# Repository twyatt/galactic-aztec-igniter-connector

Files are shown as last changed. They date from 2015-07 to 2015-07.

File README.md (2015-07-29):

# About
OSHPark PCB Top Thumbnail
OSHPark PCB Bottom Thumbnail

Custom board used to convert igniter ethernet plugs to 2-position terminal blocks for the [Galactic Aztec] rocket. The board was designed to interface with the [Galactic Aztec Raspberry Pi Add-on: Igniter] board.

Custom EagleCAD parts on this board can be found in the [SDSU Rocket Eagle Libraries].

## Wiring
The ethernet ports adhere to the following [T-568B] wiring configurations:

### Igniter
| Pin | Color | Function |
|:---:|:---:|:---:|
| 1 | Orange/White | Supply Voltage |
| 2 | Orange | Ground |
| 3 | Green/White  | Supply Voltage |
| 4 | Blue | Ground |
| 5 | Blue/White | Supply Voltage |
| 6 | Green | Ground |
| 7 | Brown/White  | Supply Voltage |
| 8 | Brown | Ground |

### Break Wire
| Pin | Color | Function |
|:---:|:---:|:---:|
| 1 | Orange/White | 3.3V |
| 2 | Orange | Signal |
| 3 | Green/White  | 3.3V |
| 4 | Blue | Signal |
| 5 | Blue/White | 3.3V |
| 6 | Green | Signal |
| 7 | Brown/White  | 3.3V |
| 8 | Brown | Signal |

## Launch
For the [Galactic Aztec April 18th, 2015 launch], a strand of solder was screwed into one side of the terminal block labeled "Break" then run thru the igniter and back to the other side of the "Break" terminal block. The "Break" terminal block does not have a polarity and simply opens or closes the connection between 3.3V and Signal.

# Bill of Materials
| Qty | Description | Part Number | Vendor |
|:---:|---|---:|---|
| 1 | Jack RJ45 CAT5/CAT5e | [380-1046-ND] | DigiKey  |
| 1 | LED Red Vf=1.8V If=2mA 0603 | [475-1195-2-ND] | DigiKey  |
| 1 | Resistor 12kΩ 1/4W 1% 0603 | [RHM12.0KADCT-ND] | DigiKey  |
| 3 | Terminal Block 0.2" Pitch Plug | [A98223-ND] | DigiKey  |
| 3 | Terminal Block 0.2" Pitch Socket | [A98235-ND] | DigiKey  |

[Galactic Aztec]: http://rocket.sdsu.edu/rockets
[Galactic Aztec Raspberry Pi Add-on: Igniter]: https://github.com/twyatt/galactic-aztec-rpi-addon-igniter
[SDSU Rocket Eagle Libraries]: https://github.com/twyatt/SDSURocket-Eagle-Libraries
[T-568B]: https://en.wikipedia.org/wiki/TIA/EIA-568#Wiring
[Galactic Aztec April 18th, 2015 launch]: https://github.com/twyatt/galactic-aztec-launch-data
[380-1046-ND]: http://www.digikey.com/product-detail/en/SS-7188-NF/380-1046-ND/388308
[475-1195-2-ND]: http://www.digikey.com/product-detail/en/LS%20L29K-H1J2-1-Z/475-1195-1-ND/810356
[RHM12.0KADCT-ND]: http://www.digikey.com/product-detail/en/ESR03EZPF1202/RHM12.0KADCT-ND/1983756
[A98223-ND]: http://www.digikey.com/product-detail/en/796634-2/A98223-ND/1827082
[A98235-ND]: http://www.digikey.com/product-detail/en/796638-2/A98235-ND/1827094

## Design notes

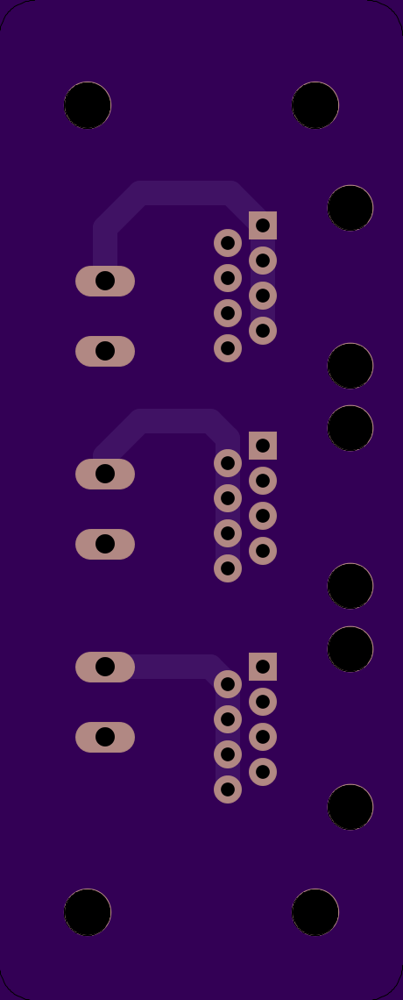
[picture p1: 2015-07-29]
artwork/bottom.png

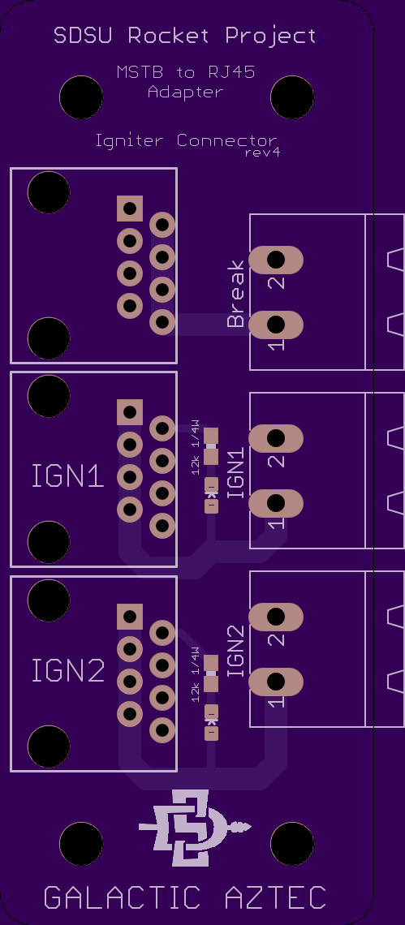
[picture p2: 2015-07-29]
artwork/top.png

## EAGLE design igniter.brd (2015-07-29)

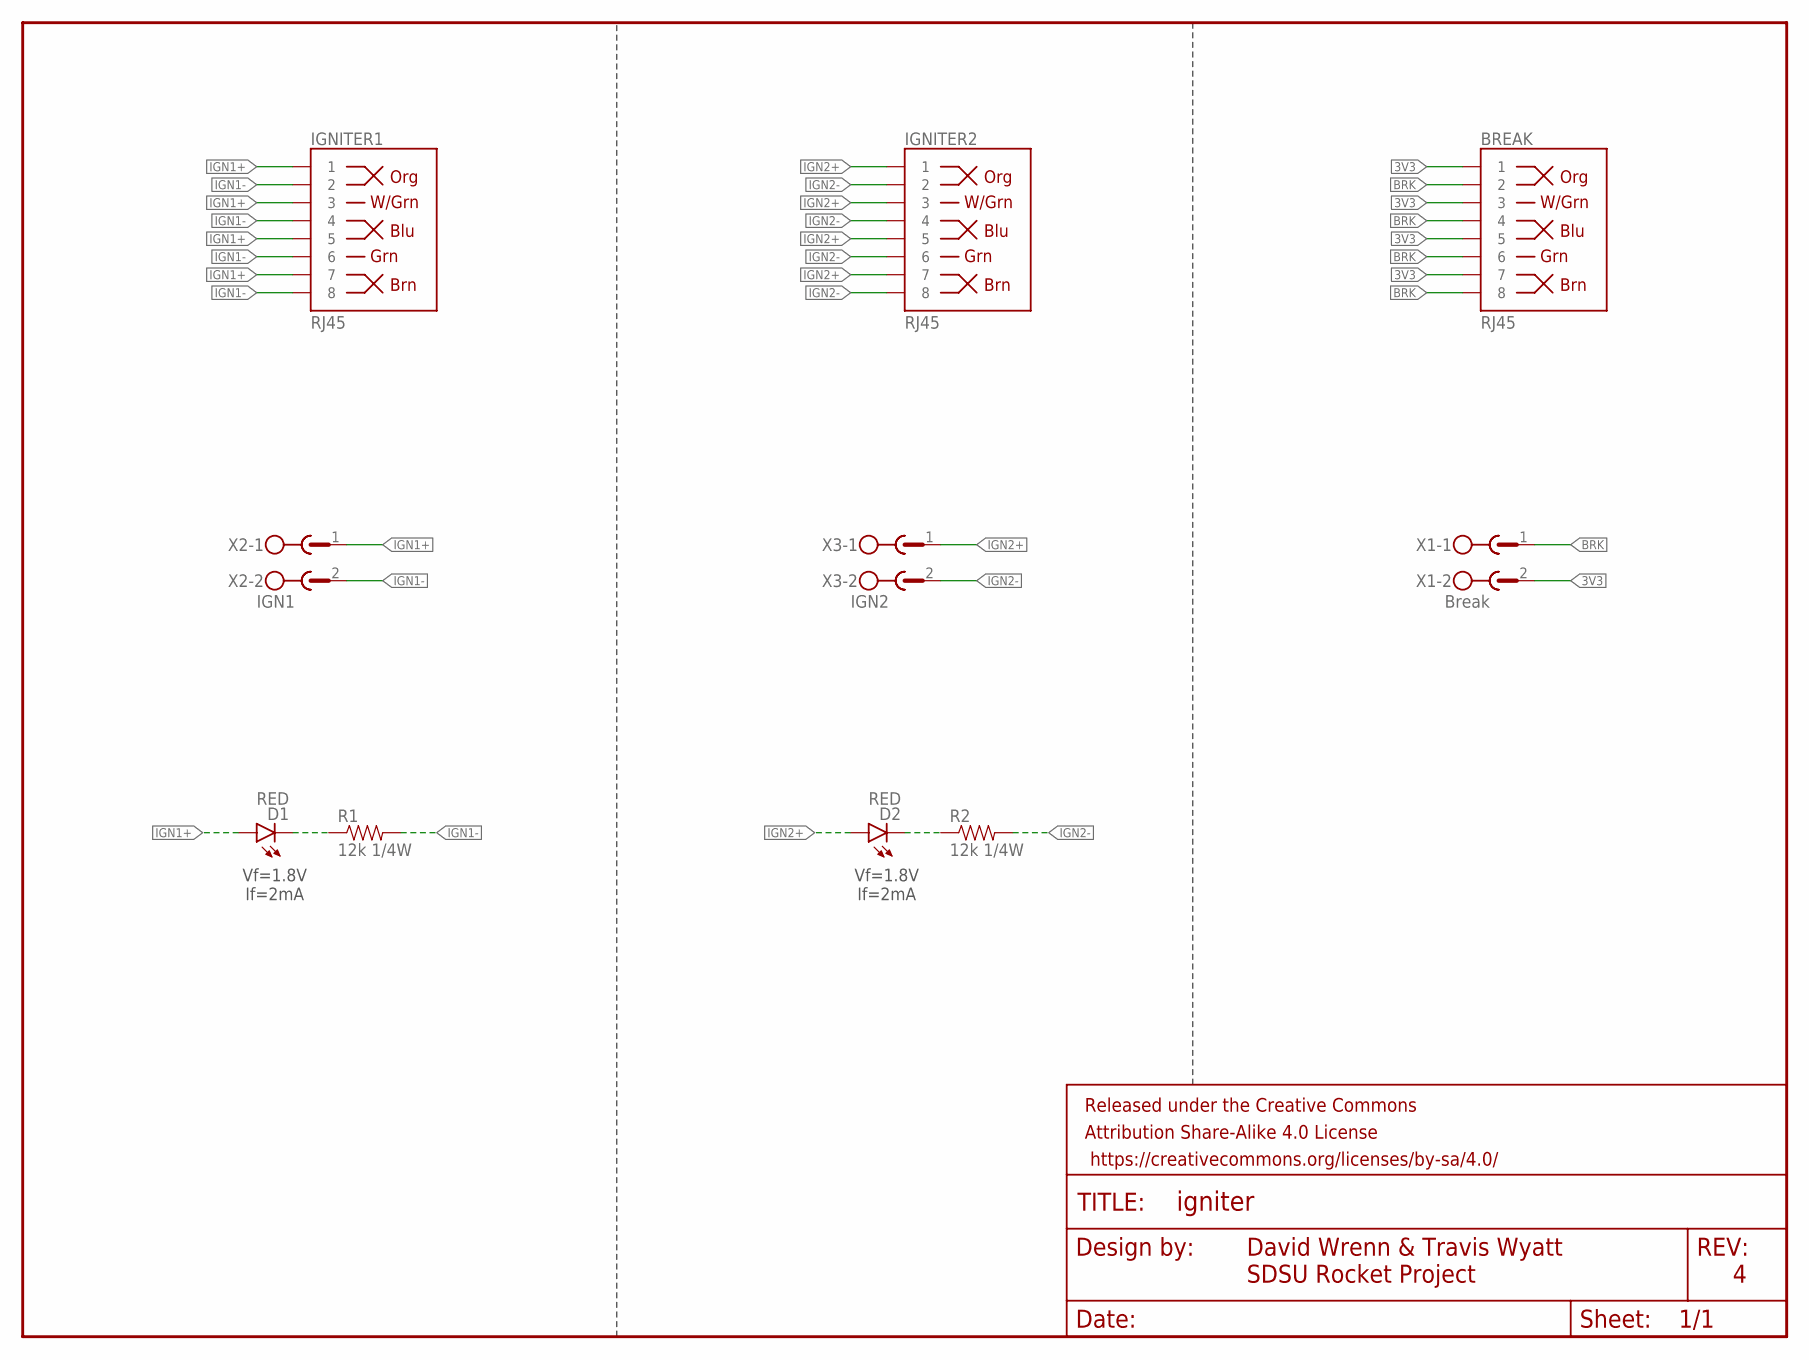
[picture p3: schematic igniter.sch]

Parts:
BREAK: RJ45; RJ45-8
D1, D2: RED; LED-0603
FRAME1: FRAME-LETTER; CREATIVE_COMMONS
IGNITER1, IGNITER2: RJ45; RJ45-8
R1, R2: 12k 1/4W; 0603-RES
X1: Break; MSTBA2
X2: IGN1; MSTBA2
X3: IGN2; MSTBA2

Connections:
3V3: BREAK.1, BREAK.3, BREAK.5, BREAK.7, X1.2
BRK: BREAK.2, BREAK.4, BREAK.6, BREAK.8, X1.1
IGN1+: D1.A, IGNITER1.1, IGNITER1.3, IGNITER1.5, IGNITER1.7, X2.1
IGN1-: IGNITER1.2, IGNITER1.4, IGNITER1.6, IGNITER1.8, R1.2, X2.2
IGN2+: D2.A, IGNITER2.1, IGNITER2.3, IGNITER2.5, IGNITER2.7, X3.1
IGN2-: IGNITER2.2, IGNITER2.4, IGNITER2.6, IGNITER2.8, R2.2, X3.2
unnamed: D1.C, R1.1
unnamed: D2.C, R2.1

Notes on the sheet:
David Wrenn & Travis Wyatt
SDSU Rocket Project
Vf=1.8V If=2mA

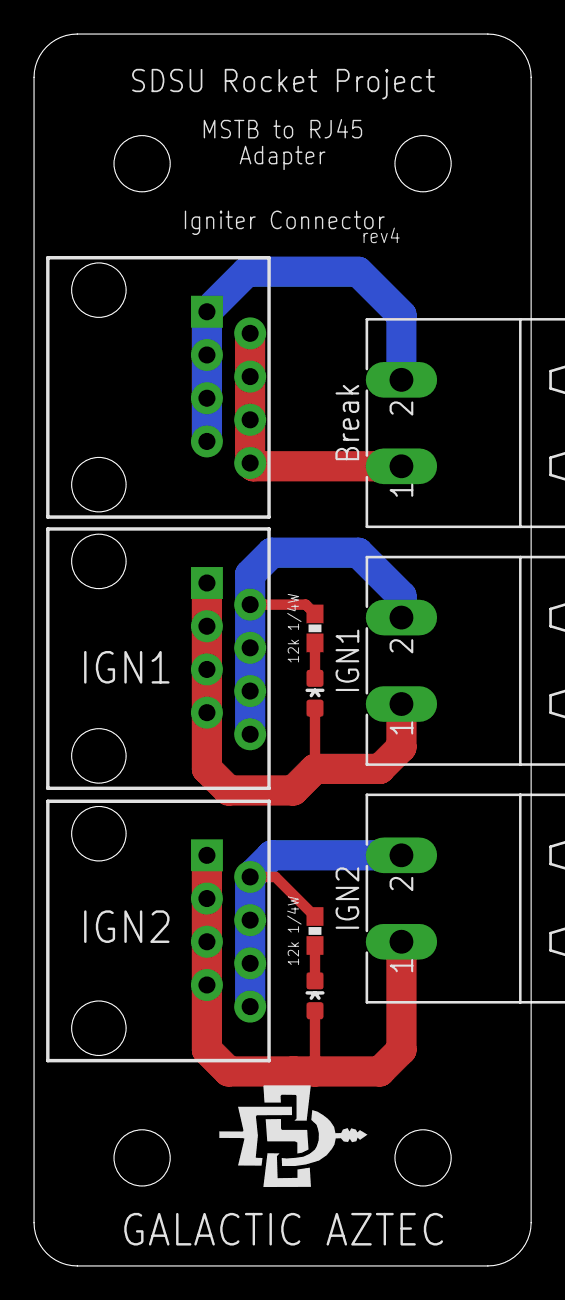
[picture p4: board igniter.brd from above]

Board: 2 copper layers, 29.2 x 72.4 mm, 15 parts (0 on the bottom side), 8 nets.

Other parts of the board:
U$1, U$2, U$3, U$4: STAND-OFF

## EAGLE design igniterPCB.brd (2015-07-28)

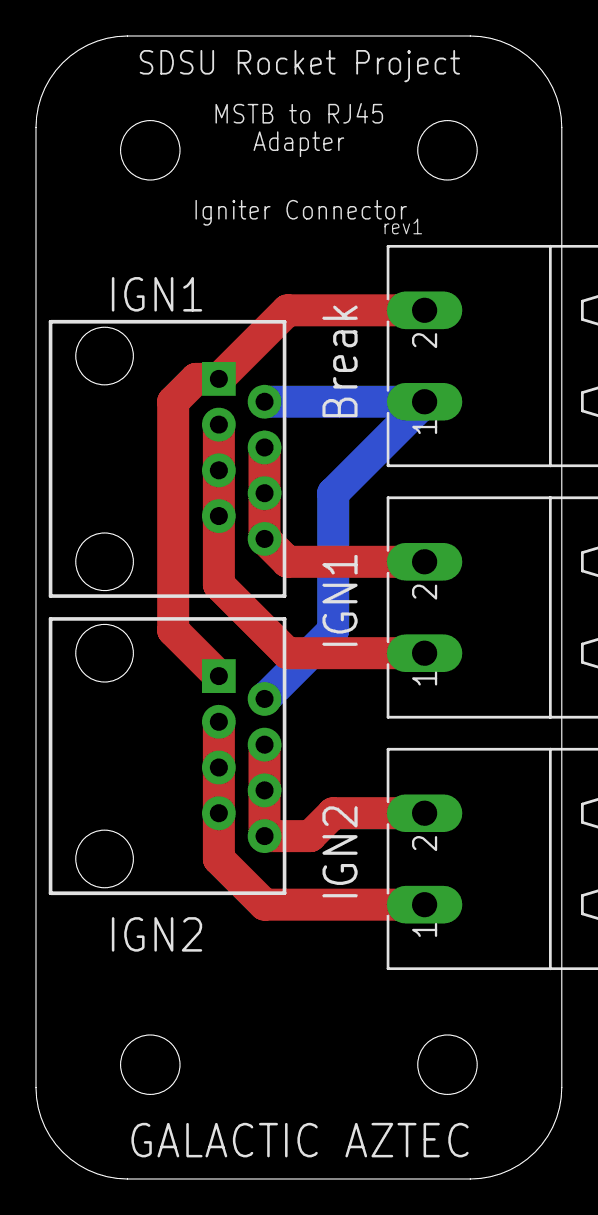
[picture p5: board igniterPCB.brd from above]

Board: 2 copper layers, 29.2 x 63.5 mm, 9 parts (0 on the bottom side), 6 nets.

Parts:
IGNITER1, IGNITER2: RJ45; RJ45-8
U$1, U$2, U$3, U$4: STAND-OFF
X1: Break; MSTBA2
X2: IGN1; MSTBA2
X3: IGN2; MSTBA2

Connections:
3V3: IGNITER1.1, IGNITER2.1, X1.2
BRK: IGNITER1.2, IGNITER2.2, X1.1
IGN1+: IGNITER1.3, IGNITER1.5, IGNITER1.7, X2.1
IGN1-: IGNITER1.4, IGNITER1.6, IGNITER1.8, X2.2
IGN2+: IGNITER2.3, IGNITER2.5, IGNITER2.7, X3.1
IGN2-: IGNITER2.4, IGNITER2.6, IGNITER2.8, X3.2

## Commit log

2015-07-28 Initial commit.
    [igniterPCB.brd, igniterPCB.sch]
2015-07-28 Added ignition status LEDs. Separated break wire from ignition wires. Added SDSU logo.
    [igniter.brd, igniter.sch, igniterPCB.sch]
2015-07-29 Updated to use more efficient LEDs. Decreased SMD resistor size to 0603.
    [igniter.brd, igniter.sch]

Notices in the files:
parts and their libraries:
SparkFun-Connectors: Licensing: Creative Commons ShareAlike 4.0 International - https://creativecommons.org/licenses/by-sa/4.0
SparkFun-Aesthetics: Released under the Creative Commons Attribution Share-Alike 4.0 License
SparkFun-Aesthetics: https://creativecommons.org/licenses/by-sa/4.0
